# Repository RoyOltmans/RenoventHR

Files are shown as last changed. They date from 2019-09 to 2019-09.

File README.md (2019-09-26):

# RenoventHR

All rights of the Mechenical ventelation system are owned by Renovent.

This is a reverse engeneered control device to remotely control and automate ventilation at home.

**Usage of this project is on your own risk.**

# Results

Some screenshot of the final endresult

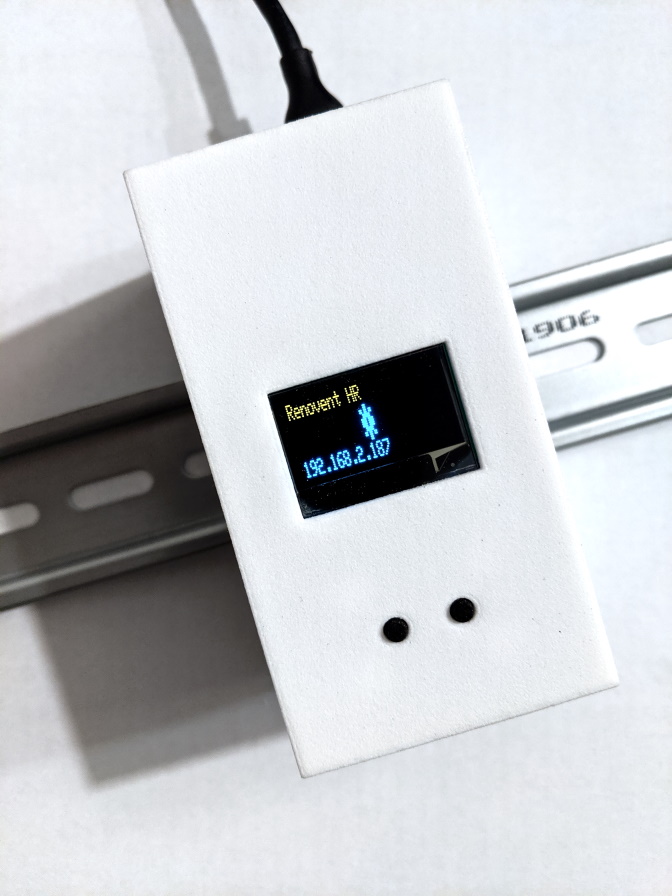
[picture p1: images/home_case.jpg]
home_case


Bottom view case

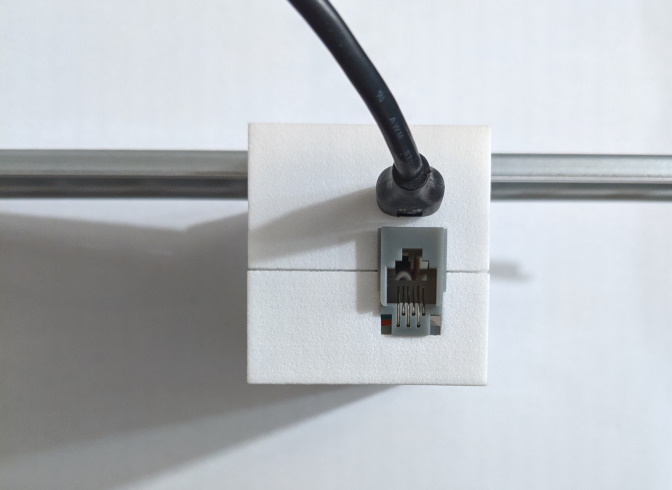
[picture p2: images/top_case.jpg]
top_case


Side view case

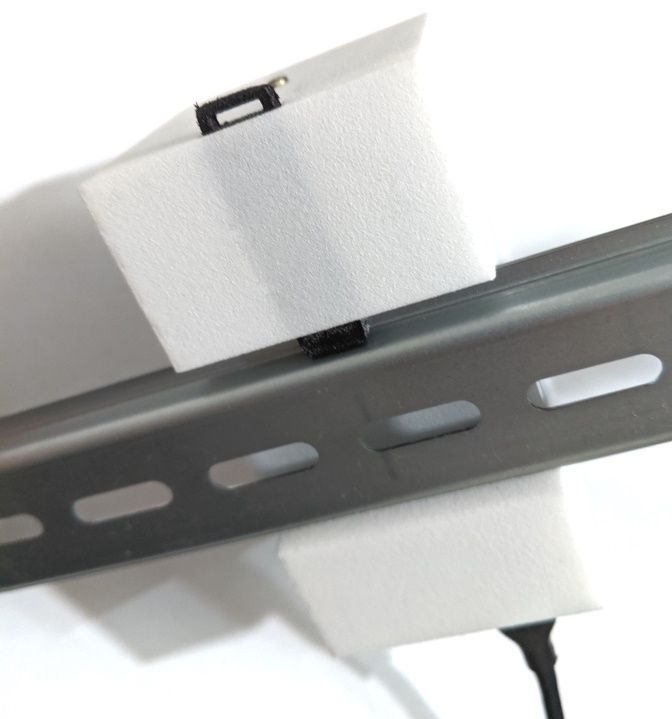
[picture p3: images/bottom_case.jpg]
bottom_case


Bottom view case

# Motivation

Connected RenoventHR Module to switch a mechanical ventilation heat recovery system from Renovent HR.

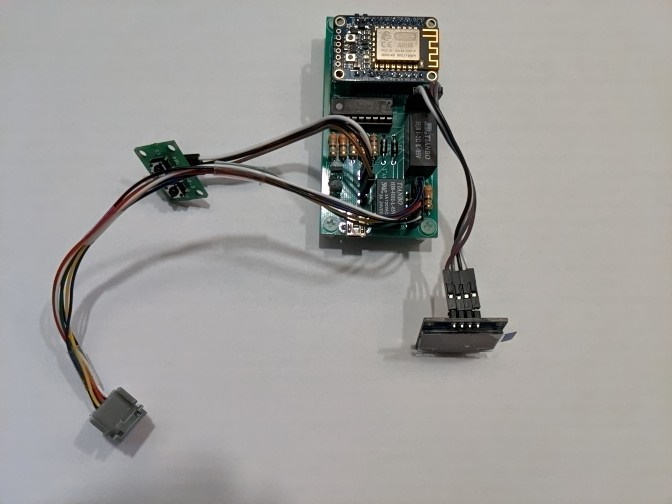
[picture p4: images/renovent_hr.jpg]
renovent_hr


I was first inspired by a friend whom wanted to switch his mechanical ventilation. He has a Renovent setup and he could use a RF solution.
That started me thinking let’s try this myself, off course I have a different setup that’s a little more complicated because of the heat recovery.

After an evening of googling I found a site of an old classmate (what a small world) Ingmar Verheij. His journey is the same as mine, but he already solved it (https://www.ingmarverheij.com/bediening-wtw-altijd-op-de-verkeerde-plek/).

He posted a solution on git but did not finish a tutorial, so I thought I could solve this quickly. After approximately half a year I can say I finished reverse engineering the setup and build the whole project with a 3D printed case (still in backorder).

I refactored the code (separated code, minified web and altered some functionality so the interaction should work) to my taste and added a few configuration hacks. 
Changes made were approximately:
 - Minified HTML (minimize System footprint)
 - Further restructured and optimized code
 - Added manual config (personal taste)
 - Separated Core, Data, Interfacing and tools (not fully)
 - Removed intmode/pinmode (secondary in total)
 - Added/rebuild button, startup, filter functions
 - Restructured code
 - Changed MCP calls intMode to pinMode
 - Added manual WIFI configuration trough config file

Also, the reverse engineering of the electronics created a lot of issues. The original part list provided left out crucial info for the relays. I almost stopped because I couldn’t fix it, after measuring everything and re-checking (going back in the books) I discovered that the pictures of the relays on the site were not the correct voltage. The part list in the bottom are all the correct parts. Be careful with the rj12 jack, if you use a different form factor it maybe will not fit in the case (adjust the case according with fusion 360).

So, to let you wait further let’s go into the build.

# Building the code
The code needs to be compiled with preferably the Arduino IDE version 2.4.1 below the settings:

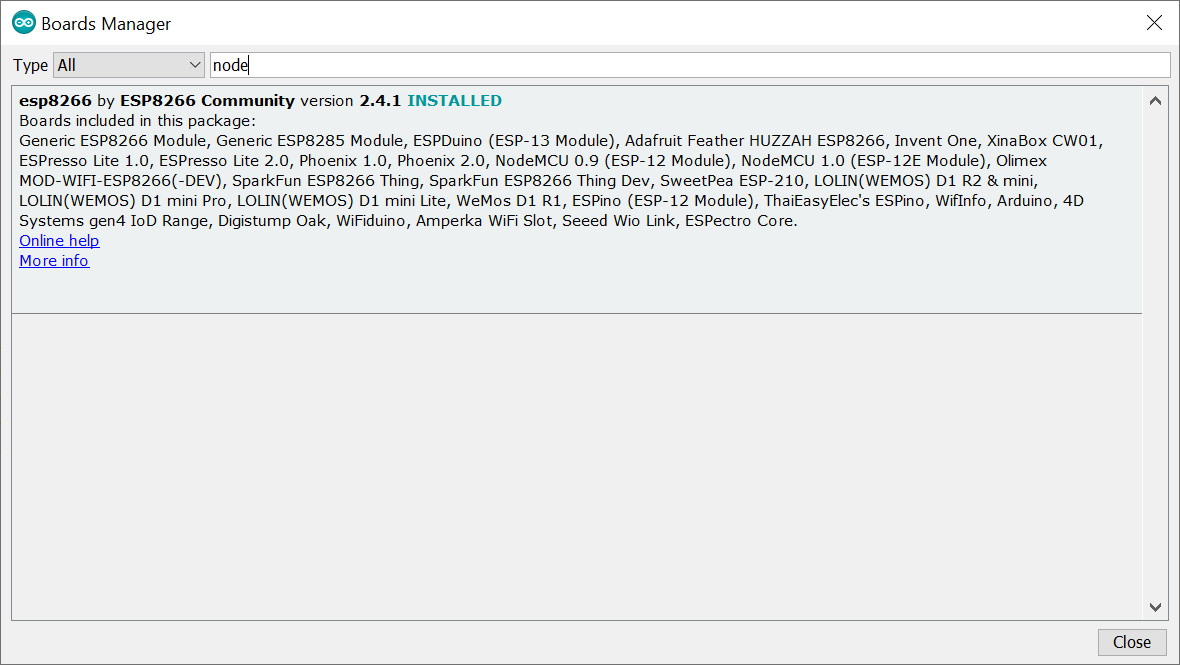
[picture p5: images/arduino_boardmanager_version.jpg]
arduino_boardmanager_version
 
Set the compiler to use the right version 2.4.1 of nodemcu ESP firmware build tools. 

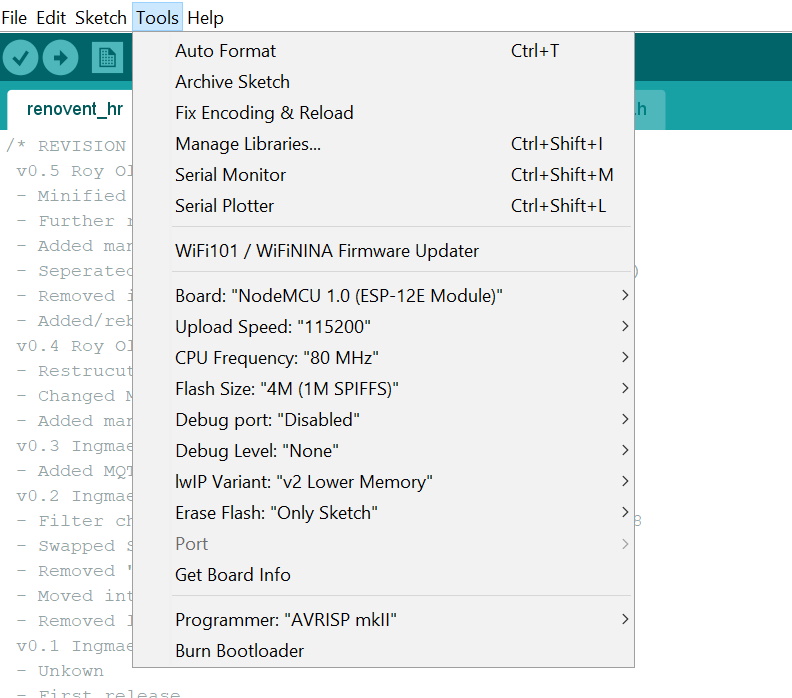
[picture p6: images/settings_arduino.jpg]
settings_arduino
 
Set the correct settings for the HUZZAH board for uploading the compiled code.

I also added the working libraries, after a lot of juggling I figured these are the used standard libs:
https://github.com/RoyOltmans/RenoventHR/tree/master/lib

For flashing the HUZZAH via a normal usb cable use the correct sequence of buttons to get in program mode. If I remember correctly, GPIO0 must be low while booting: press and hold the reset button. press and hold the program button. release the reset button, the HUZZAH will boot in program mode.

# Case
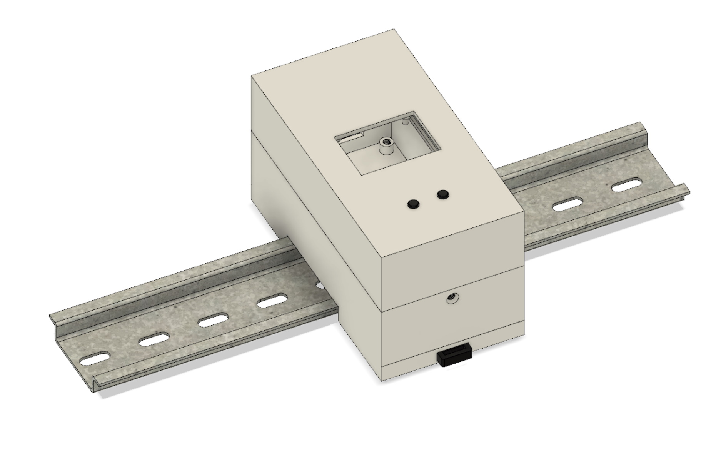
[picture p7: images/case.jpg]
case
 To build the case use the following STL files in this location https://github.com/RoyOltmans/RenoventHR/tree/master/bin/3D%20Models%20STL

I have also added the Fusion 360 (from autodesk https://www.autodesk.com/products/fusion-360/students-teachers-educators) file so you can edit the case (please do not judge my CAD skills).

You will need to get a DIN rail to mount the case on and if you prefer as I do a 5-volt din rail power source. 
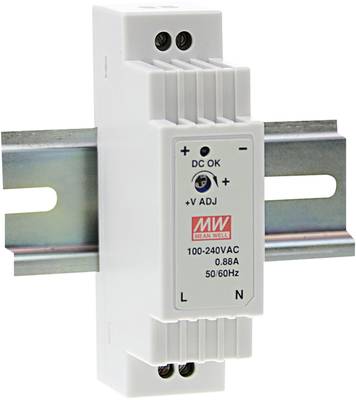
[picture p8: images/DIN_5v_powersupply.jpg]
DIN_5v_powersupply


See Mean Well DR-15-5 DIN-rail 5 V/DC2.4A 12W (https://s.click.aliexpress.com/e/mliRreY0)

# PCB's
To build the project firstly you need to order the PCB design via for example seeed studio, they can process eagle schema (in the repository).

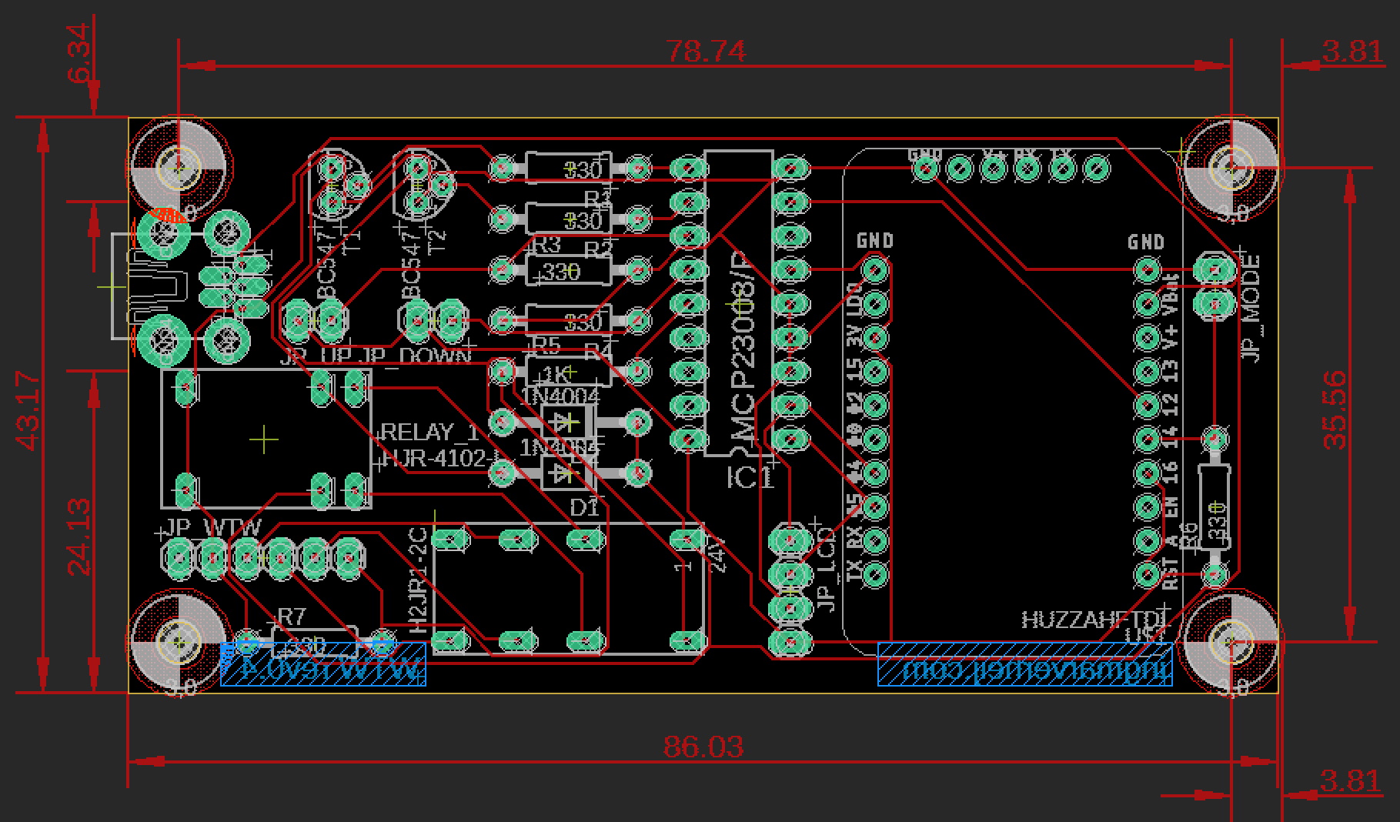
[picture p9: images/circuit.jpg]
circuit

The primary pcb:
https://github.com/RoyOltmans/RenoventHR/tree/master/pcb/EAGLE/RenoventHR%20v0.4

I ordered this board on https://www.seeedstudio.com/ was very happy with end result and the price.
To edit the board you will need Eagle (from autodesk https://www.autodesk.com/products/eagle/free-download) you can download this freely.

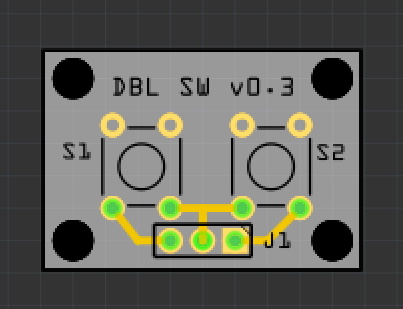
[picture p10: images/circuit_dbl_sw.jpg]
circuit_dbl_sw


The double switch pcb:
https://github.com/RoyOltmans/RenoventHR/tree/master/pcb/Fritzing/Double%20Tactile%20Switch%20v0.3

I ordered this board directly via the tool, also very good service, price and quick (https://aisler.net/partners/fritzing).
To edit this board you will need fritzing you can download this for free (https://fritzing.org/home/).

# Pinlayout

Every connector PCB printed text should be horizontally aligned to number the pins, pin 1 itterating every pin plus 1 afterwards are the pin numbers.

LCD pinlayout
```
-----------------
JP_LCD PINS
Pin   1   2   3   4
      |   |   |   |
Pin  VCC GND SCL SDA
Connected to LCD 
-----------------
```
Switch Pinlayout
```
-----------------
JP_UP PINS:

Pin    1         2 
       |         |
Pin    -     Left Pin
JP_1 on DBL SW PCB
-----------------
JP_DOWN PINS
Pin    1         2 
       |         |
Pin Center Pin  Right Pin
JP_1 on DBL SW PCB
-----------------
```

WTW RJ12 connector
```
-----------------
JP_WTW PINS
  1     2    3    4      5    6
  |     |    |    |      |    |
White Black Red Green Yellow Blue
RJ12 Color coding
-----------------
```

# Tools
Personally, I solder with a soldering tip Pencil shape size 0.4 mm, this worked perfectly. 

Good tools are half of the work, new tip, good soldering paste (wire), magnifying glass etc.

# SMART-HUB - Home Assistant
For details on connecting to the HA, I suggest looking at the site of Ingmar https://www.ingmarverheij.com/built-smart-heat-recovery-system/

Be careful I changed the MQTT paths and these are accessible via the config file. I will repost them below:
```
/*-------------------MQTT topics-------------------*/
#define Gateway_Name "RenoventHR"
#define Base_Topic "home/"
#define MQTT_GetState_Topic Base_Topic Gateway_Name "/getWTWstate"
#define MQTT_State_Topic Base_Topic Gateway_Name "/wtwState"
#define MQTT_FilterState_Topic Base_Topic Gateway_Name "/changeFilter"
#define MQTT_SetState_Topic Base_Topic Gateway_Name "/setWTWstate"

#define MQTT_Standard_Topic Base_Topic Gateway_Name
```

After some tinkering I have decided to add a short totorial of the implementation in Home Assistant. Notice you will MQTT to get this fully operational.

Firstly I must give credits to **Ingmar Verheij** for researching the HA connectivity and the custom fan card support for HA by **finity69x2**, see his github for the original JS script *https://github.com/finity69x2/fan-control-entity-row*.

To start of, I am using a older version of **HA version 0.86.4**. *Be aware this can work differently on your version of HA.*

Firstly you will need to upload a javascript in to the `www` folder of the configuration root of home-assistant (your .yaml are also located here). If this folder does not exist create it. 

On linux you can do the following steps:
```
mkdir www
wget https://raw.githubusercontent.com/RoyOltmans/RenoventHR/master/code/Home%20Assistant/www/fan-control-entity-row.js
```

After you have done this on older version of HA you need to edit ui-lovelace.yaml (this does not work if you created a lovelace interactive version.

In ui-lovelace.yaml you will need to add the following below `resources`
```
  - url: /local/fan-control-entity-row.js
    type: js
```

If this does not work you can try to open the raw editor of lovelace and add the following at the top: 
```
resources:
  - type: js
    url: /local/fan-control-entity-row.js
```

Once your finished add a new file to the configuration root of home assistant. Use the follwoing command for that
```
wget https://raw.githubusercontent.com/RoyOltmans/RenoventHR/master/code/Home%20Assistant/fan.yaml
```

Onze you have done all these staps restart home assistant fully, this will reload and add the fan control of the WTW via MQTT.

Onze you have finished this you can add the following card to your lovelace dashboad. You can do this by toggling the editor and adding a card manualy via the lovelace configurator in HA.

```
entities:
  - customTheme: true
    entity: fan.wtw_mechanic_ventilation
    name: WTW Renovent HR
    type: 'custom:fan-control-entity-row'
    show_header_toggle: false
title: Mechinical Ventilation
type: entities
```

Below a screenshot of the card in Home Assistant.
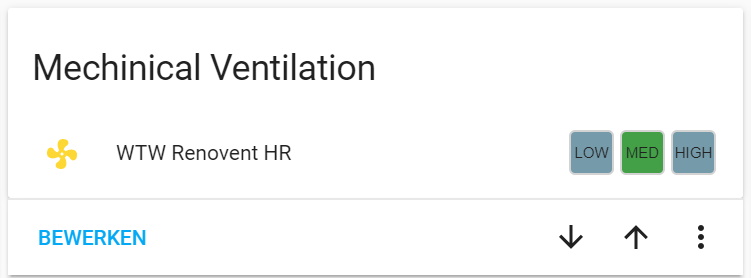
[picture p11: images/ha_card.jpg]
ha card


Once you have added the fan you can control the fan levels via sesnors and automations you have designed yourself. Ingmar also described a way to add a notification for cleaning the filters. Please see his tutorial for further info.

# Configuration and Software
For configurations, you can follow the description on https://www.ingmarverheij.com/built-smart-heat-recovery-system/
The software as written by Ingmar is still operational, you can interact directly with the device. Or you can couple it through a smart hub via MQTT as described above.

Or edit the config.h file adding your personal configurations, below you will find the details of the config.h:
```
/*-------------------General----------------------*/
const char* Version = "0.5";

/*-------------------WIFI Settings----------------*/
String APssid = "SSID WIFI";
String APpassword = "PASSWORD WIFI";

/*-------------------MQTT Settings-------------------*/
String mqtt_user = "your_username"; // not compulsory only if your broker needs authentication
String mqtt_pass = "your_password"; // not compulsory only if your broker needs authentication
String mqtt_server = "MQTT SERVER NAME or IP";
long mqtt_port = strtol("1883",NULL,10);

/*-------------------MQTT topics-------------------*/
#define Gateway_Name "RenoventHR"
#define Base_Topic "home/"
#define MQTT_GetState_Topic Base_Topic Gateway_Name "/getWTWstate"
#define MQTT_State_Topic Base_Topic Gateway_Name "/wtwState"
#define MQTT_FilterState_Topic Base_Topic Gateway_Name "/changeFilter"
#define MQTT_SetState_Topic Base_Topic Gateway_Name "/setWTWstate"

#define MQTT_Standard_Topic Base_Topic Gateway_Name
```

# Part list
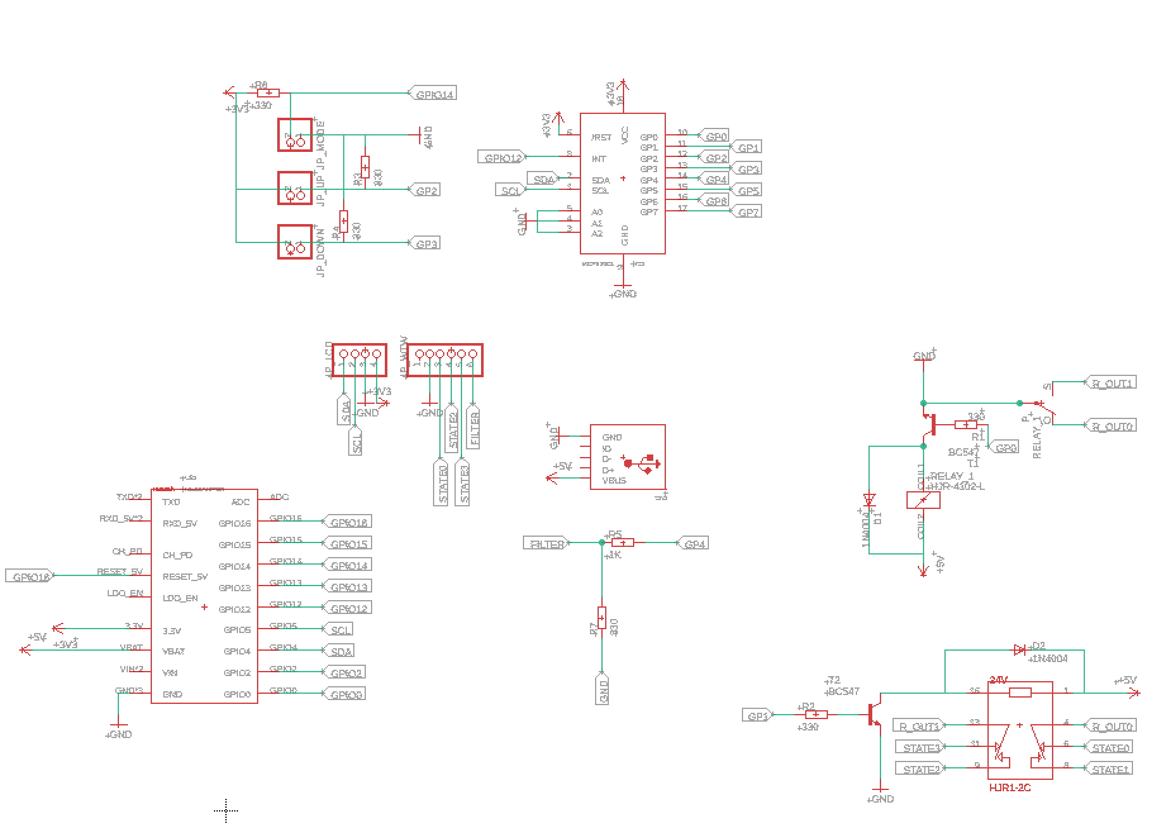
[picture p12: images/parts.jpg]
parts

- hjr-4102-l 1x Miniature relay HJR-4102-L-05VDC-S-Z (order at Conrad (EU))
- hjr1-2c 1x Miniature relay HJR1-2C-L-05VDC (order at Conrad (EU))
- ic-18 1x IC base 18 pins (order at Conrad (EU))
- jumper 1x Jumper black open (Jumper zwart open) (order at Conrad (EU))
- resistor330 6x Carbon film resistance 0,5W 0411 330Ohm (Koolfilmweerstand 330Ω Axiaal bedraad 0411 0.5 W 5) (order at Conrad (EU))
- resistor1k 1x Carbon film resistance 0,5W 0411 1KOhm (Koolfilmweerstand 1 kΩ Axiaal bedraad 0411 0.5 W 5 ) (order at Conrad (EU))
- connector 1x Bus, horizontal installation MUB1B5W 1 Port econ connect (order at Conrad (EU))
- maleheader1x Würth Elektronik Male header (order at Conrad (EU))
- femaleheader1x Würth Elektronik Female header (standard) WR-PHD Total poles 10 grid size: 2.54 mm 61301011821 (order at Conrad (EU))
- mcp230081x Microchip Technology MCP23008-E/P Interface-IC - I/O expansion POR I²C 1.7 MHz PDIP-18 (order at Conrad (EU))
- bc547a 2x Diotec BC547A Transistor (BJT) - discreet TO-92 1 NPN (order at Conrad (EU))
- 1n4004 2x Diotec Si-rectifier diode 1N4004 DO-204AL 400 V 1 A (order at Conrad (EU))
- adafruit_HUZZAH_ESP8266_lq1x Adafruit HUZZAH ESP8266 Breakout (https://www.adafruit.com/product/2471)
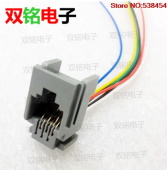
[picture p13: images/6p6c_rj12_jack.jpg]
6p6c_rj12_jack
-  1x rj12 jack with cables and sleeve for case (https://s.click.aliexpress.com/e/ExAocZHe)
- 096inch_128X64_YellowBlue_OLED_Display_Module 1x 0.96inch 128X64 Yellow Blue OLED Display Module (https://s.click.aliexpress.com/e/39m65cSM)
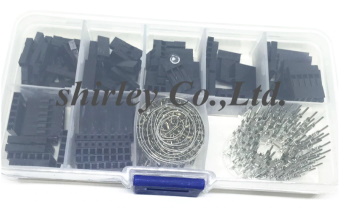
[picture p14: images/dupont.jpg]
dupont
-  Dupont Wire Jumper Pin Header Connector (https://s.click.aliexpress.com/e/3WbYzW3I)
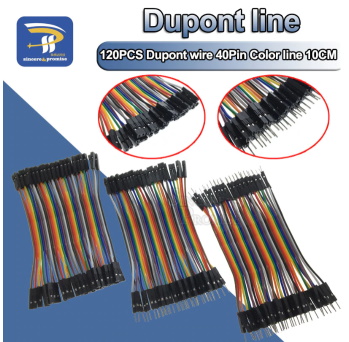
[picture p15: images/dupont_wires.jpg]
dupont_wires
- Dupont Wires (https://s.click.aliexpress.com/e/KMFFxgfe)
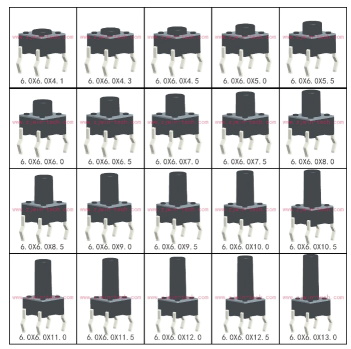
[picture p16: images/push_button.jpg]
push_button
-  A generic pushbutton (https://s.click.aliexpress.com/e/kaTmlRJw)

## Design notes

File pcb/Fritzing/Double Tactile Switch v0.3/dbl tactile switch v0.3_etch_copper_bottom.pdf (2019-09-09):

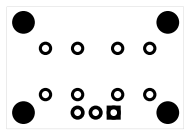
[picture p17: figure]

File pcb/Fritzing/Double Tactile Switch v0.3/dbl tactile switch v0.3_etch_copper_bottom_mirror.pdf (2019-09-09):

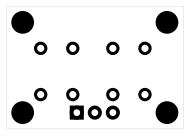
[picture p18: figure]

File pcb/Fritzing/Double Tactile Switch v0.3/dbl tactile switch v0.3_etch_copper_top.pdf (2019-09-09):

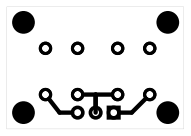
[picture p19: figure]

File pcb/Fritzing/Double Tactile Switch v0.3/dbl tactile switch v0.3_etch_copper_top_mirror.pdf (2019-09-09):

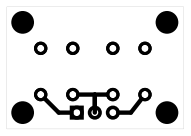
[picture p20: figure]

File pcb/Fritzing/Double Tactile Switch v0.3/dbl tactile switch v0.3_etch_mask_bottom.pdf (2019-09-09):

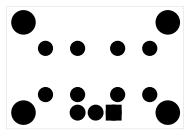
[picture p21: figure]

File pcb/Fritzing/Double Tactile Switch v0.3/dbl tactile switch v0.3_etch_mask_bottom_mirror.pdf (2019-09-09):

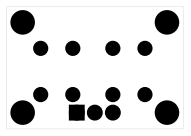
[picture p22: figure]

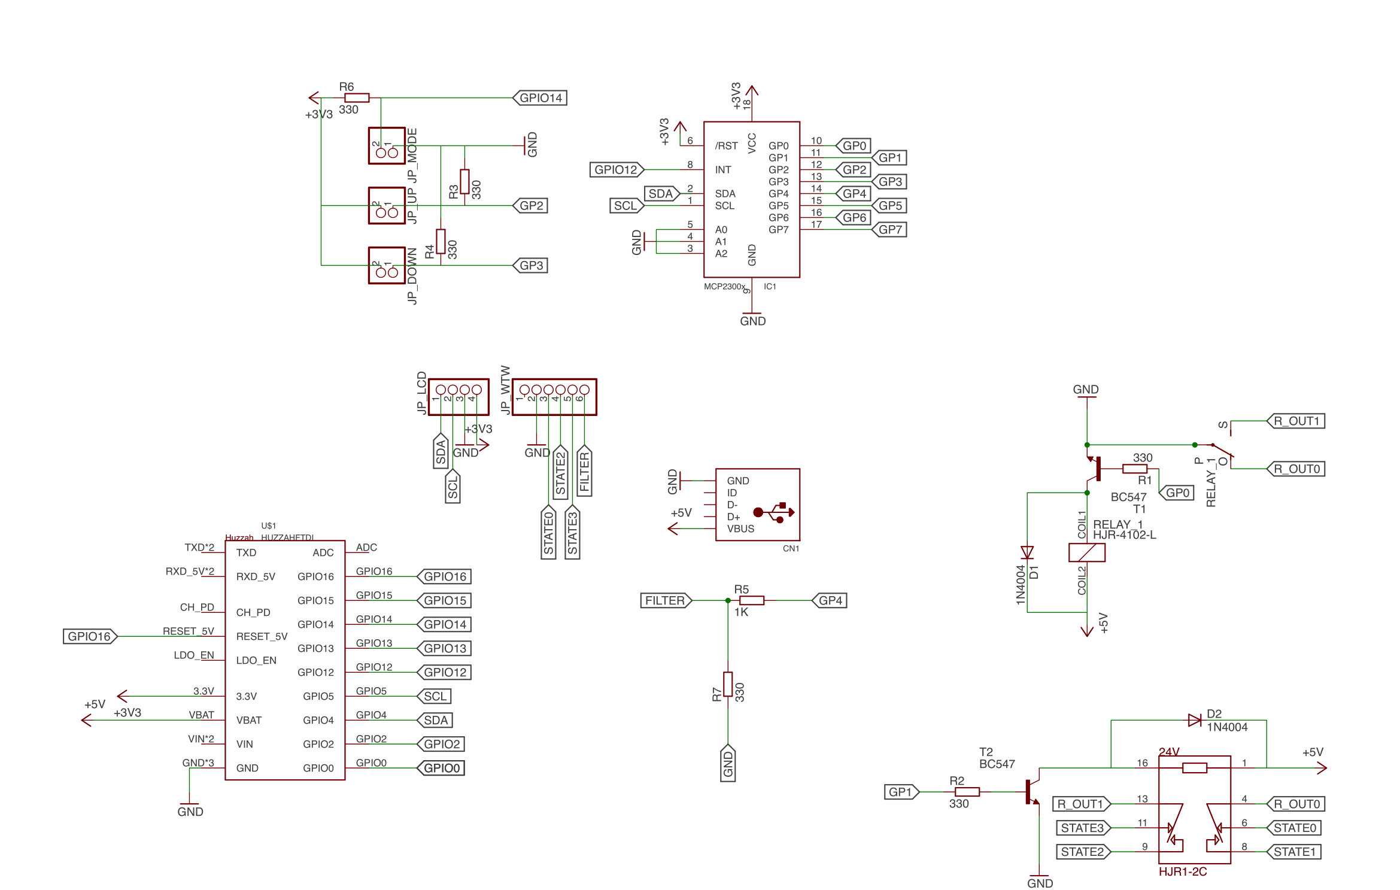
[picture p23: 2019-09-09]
pcb/EAGLE/RenoventHR v0.4/Image-Schematic.png

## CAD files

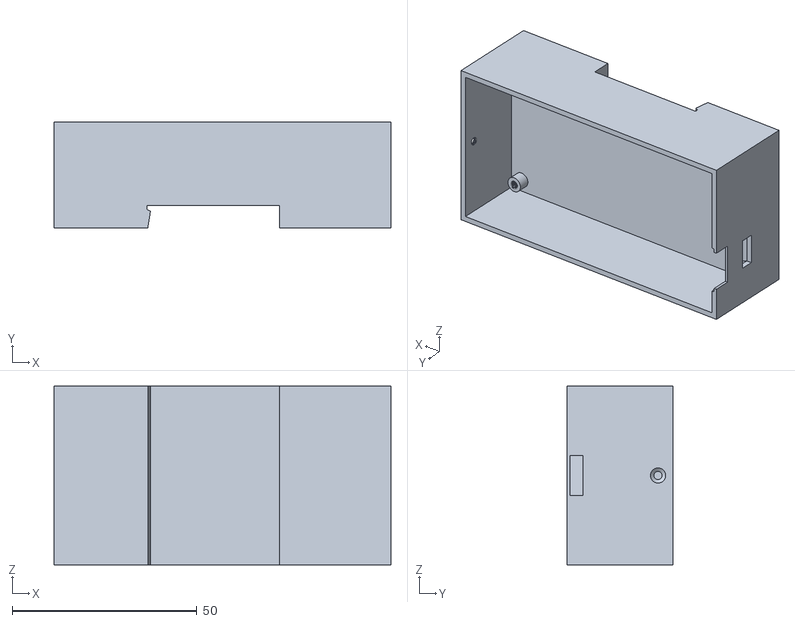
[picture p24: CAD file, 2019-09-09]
bin/3D Models STL/Bottom Case.stl
91.2 x 28.6 x 48.5

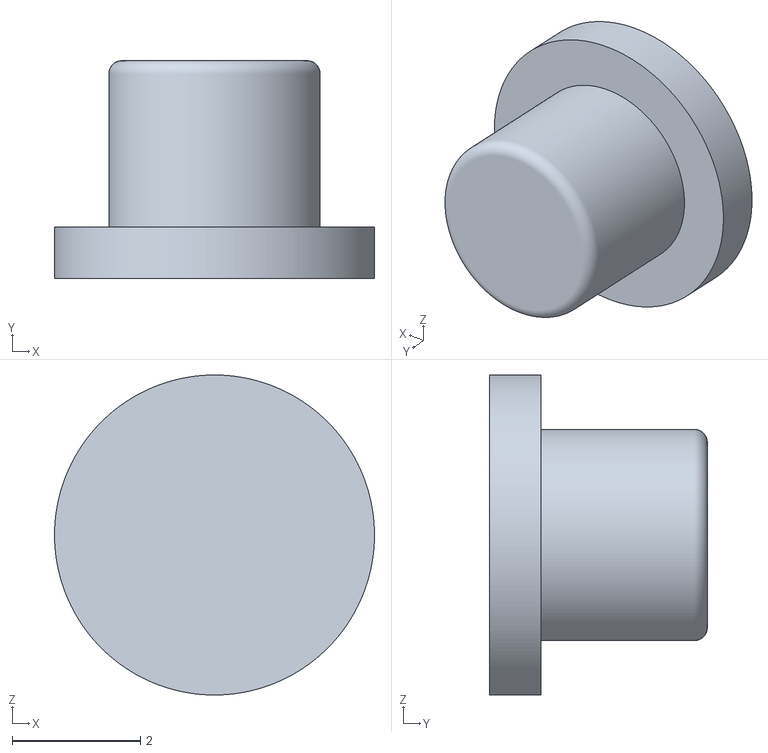
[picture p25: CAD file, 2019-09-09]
bin/3D Models STL/Button Left.stl
5.00 x 3.40 x 5.00

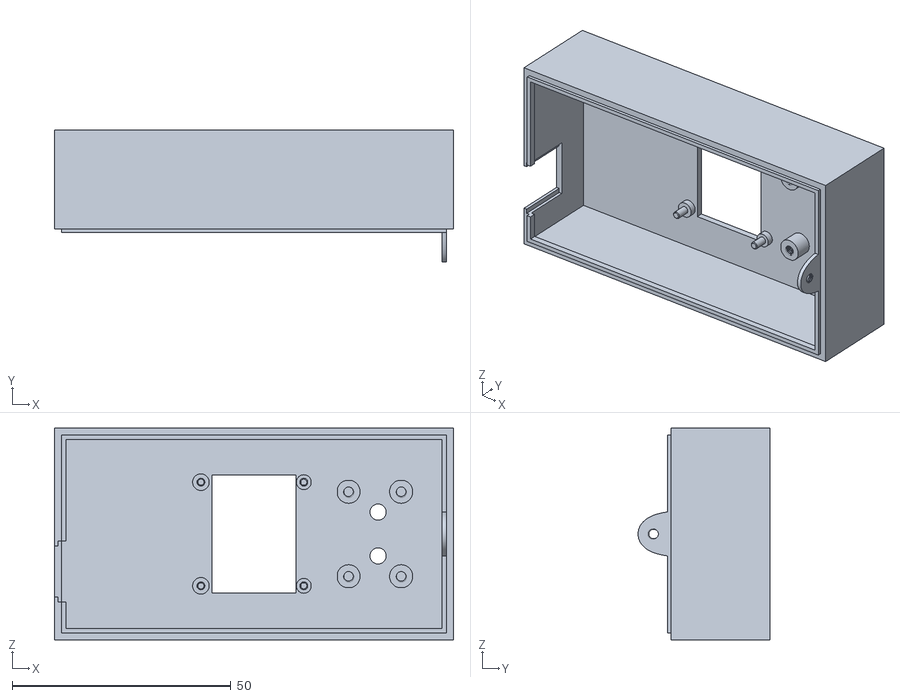
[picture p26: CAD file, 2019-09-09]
bin/3D Models STL/Top Case.stl
91.2 x 30.2 x 48.5

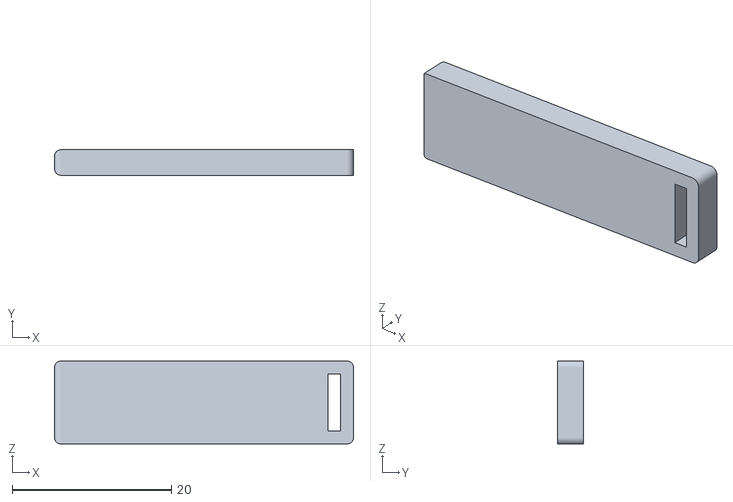
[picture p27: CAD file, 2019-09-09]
bin/3D Models STL/Clip.stl
37.5 x 3.20 x 10.4

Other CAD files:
bin/3D Models STL/Button Right.stl
3D model/Renovent HR Case Version 3.1 v3.f3d

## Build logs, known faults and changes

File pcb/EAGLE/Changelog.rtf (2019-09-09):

Rev 0.4
- Added pull down resistor for FILTER
- Changed package of mini USB to match physical layout

Rev 0.3
- Swapped STATE2 and STATE3 (just for visuals, was already done in code)

Rev 0.2
- Swapped collector and emitter on T1 and T2 (to relay)
- Added mini-USB +5V bus for power (VBAT) and relays
- Renumbered the resistors (was unlogical)
- Included 3mm drill holes
- Added text on back - ingmarverheij.com
- Added text on back - WTW rev0.2
(- Used RJC-4102 instead of RJC-4102-E)

Rev 0.1
- Initial version

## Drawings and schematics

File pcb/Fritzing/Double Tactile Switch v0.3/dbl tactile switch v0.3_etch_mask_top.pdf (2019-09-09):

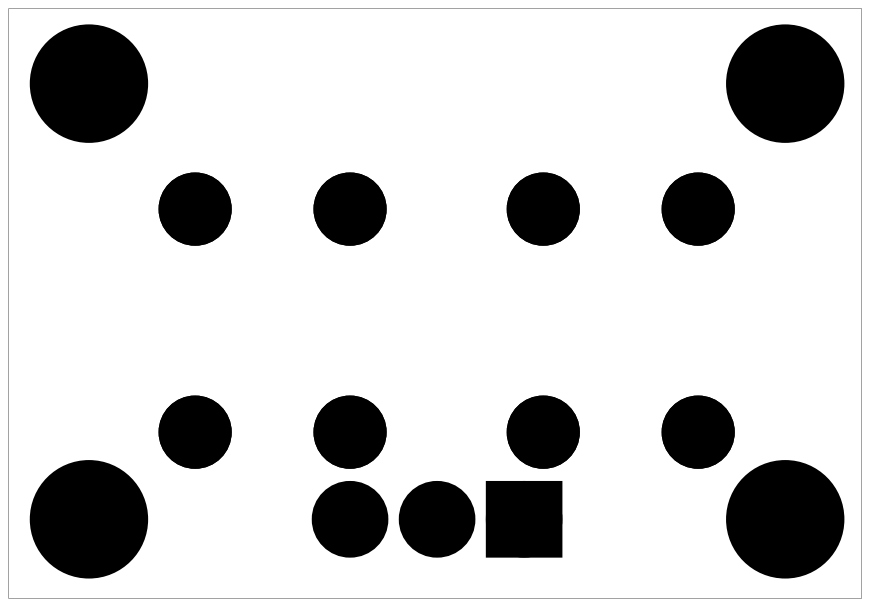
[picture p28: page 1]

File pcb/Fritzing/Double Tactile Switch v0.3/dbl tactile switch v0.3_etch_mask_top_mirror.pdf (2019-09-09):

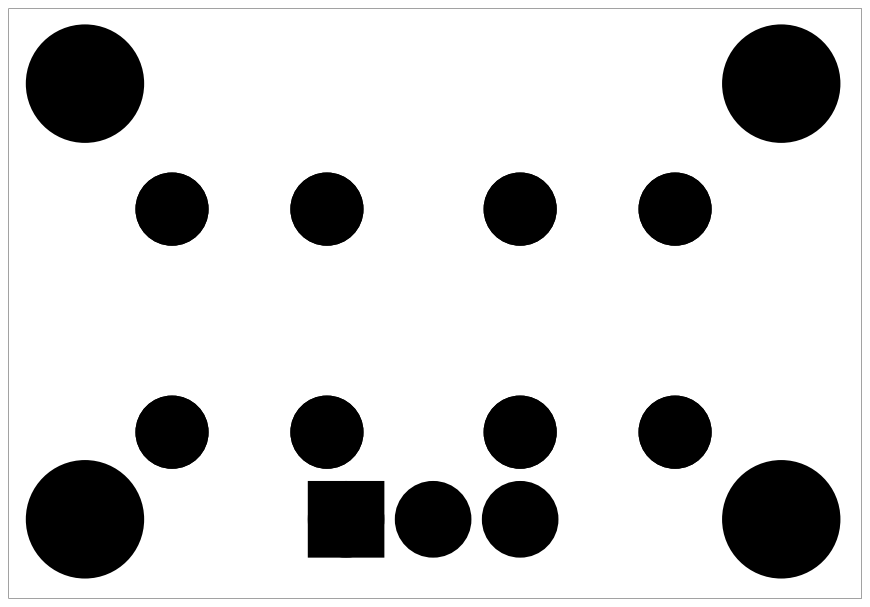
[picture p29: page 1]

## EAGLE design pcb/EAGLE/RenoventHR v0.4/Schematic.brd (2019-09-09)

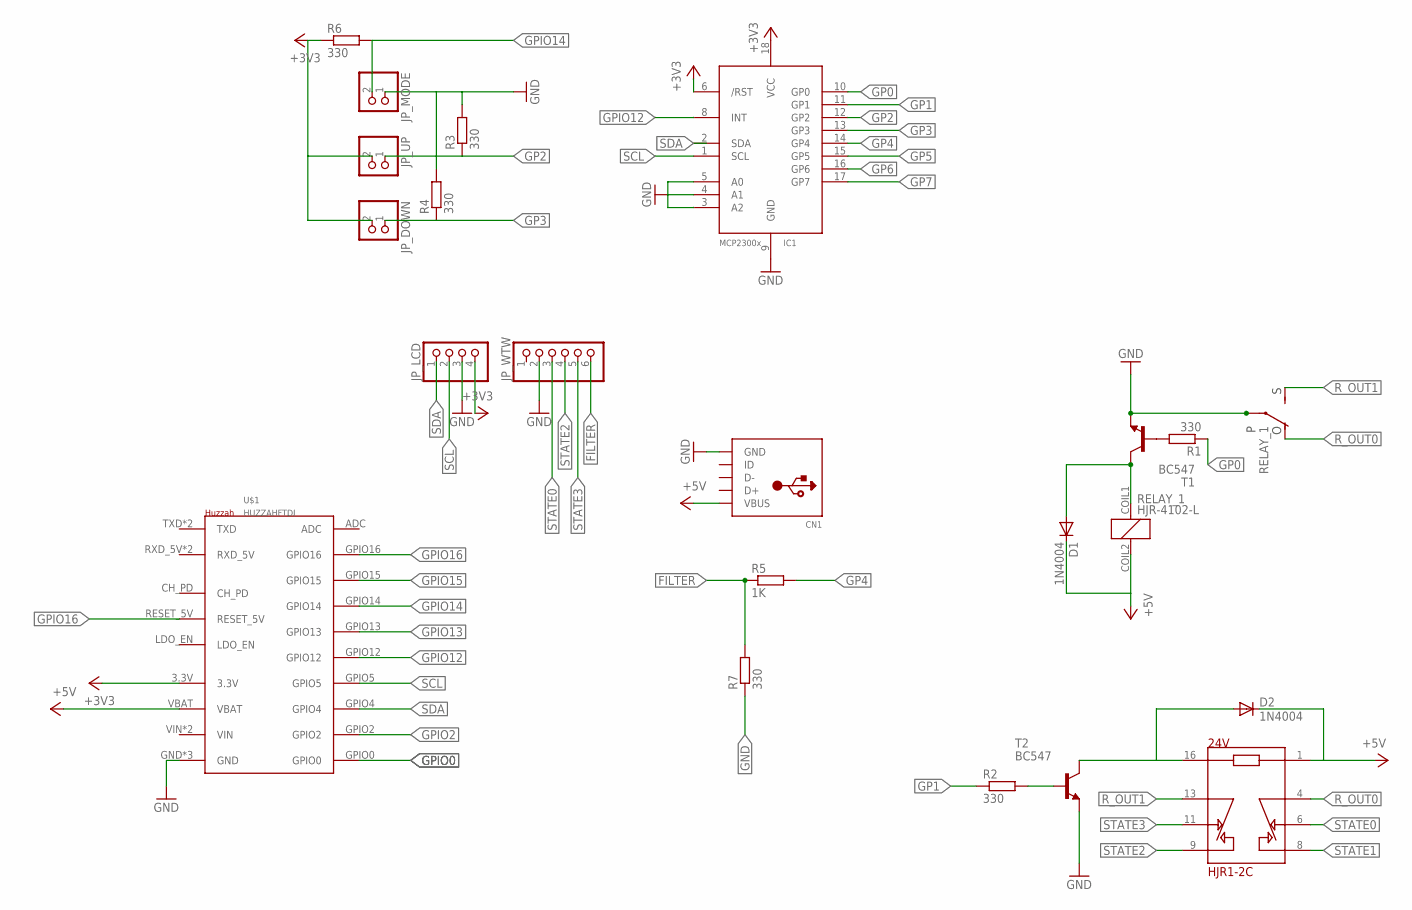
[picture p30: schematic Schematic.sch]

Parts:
CN1: USBTHM; USB-MINIB-THM
D1, D2: 1N4004; DO41-10
IC1: MCP23008/P; DIL18
JP_DOWN: PINHD-1X2; 1X02
JP_LCD: PINHD-1X4; 1X04
JP_MODE: PINHD-1X2; 1X02
JP_UP: PINHD-1X2; 1X02
JP_WTW: PINHD-1X6; 1X06
R1, R2, R3, R4, R6, R7: 330; 0207/10
R5: 1K; 0207/10
RELAY_1: HJR-4102-L; HJR4102
RELAY_2: HJR1-2C
T1, T2: BC547; TO92
U$1: HUZZAHFTDI; HUZZAH-FULL

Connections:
+3V3: IC1.6 (/RST), IC1.18 (VCC), JP_DOWN.2, JP_LCD.4, JP_UP.2, R6.1, U$1.3.3V
+5V: CN1.VBUS, D1.C, D2.C, RELAY_1.COIL2 (2), RELAY_2.1, U$1.VBAT
FILTER: JP_WTW.6, R5.1, R7.2
GND: CN1.GND, IC1.3 (A2), IC1.4 (A1), IC1.5 (A0), IC1.9 (GND), JP_LCD.3, JP_MODE.1, JP_WTW.2, R3.2, R4.2, R7.1, RELAY_1.CENTER1, RELAY_1.CENTER2 (P2), T1.1 (E), T2.1 (E), U$1.GND, U$1.GND2 (GND), U$1.GND3 (GND)
GP0: IC1.10 (GP0), R1.1
GP1: IC1.11 (GP1), R2.1
GP2: IC1.12 (GP2), JP_UP.1, R3.1
GP3: IC1.13 (GP3), JP_DOWN.1, R4.1
GP4: IC1.14 (GP4), R5.2
GP5: IC1.15 (GP5)
GP6: IC1.16 (GP6)
GP7: IC1.17 (GP7)
GPIO0: U$1.GPIO0
GPIO2: U$1.GPIO2
GPIO12: IC1.8 (INT), U$1.GPIO12
GPIO13: U$1.GPIO13
GPIO14: JP_MODE.2, R6.2, U$1.GPIO14
GPIO15: U$1.GPIO15
GPIO16: U$1.GPIO16, U$1.RESET_5V
unnamed: R1.2, T1.2 (B)
unnamed: R2.2, T2.2 (B)
R_OUT0: RELAY_1.CON2OPTION (O), RELAY_2.4
R_OUT1: RELAY_1.CON1DEFAULT (S), RELAY_2.13
SCL: IC1.1 (SCL), JP_LCD.2, U$1.GPIO5
SDA: IC1.2 (SDA), JP_LCD.1, U$1.GPIO4
STATE0: JP_WTW.3, RELAY_2.6
STATE1: RELAY_2.8
STATE2: JP_WTW.4, RELAY_2.9
STATE3: JP_WTW.5, RELAY_2.11
T1_RELAY1: D1.A, RELAY_1.COIL1 (1), T1.3 (C)
T2_RELAY2: D2.A, RELAY_2.16, T2.3 (C)

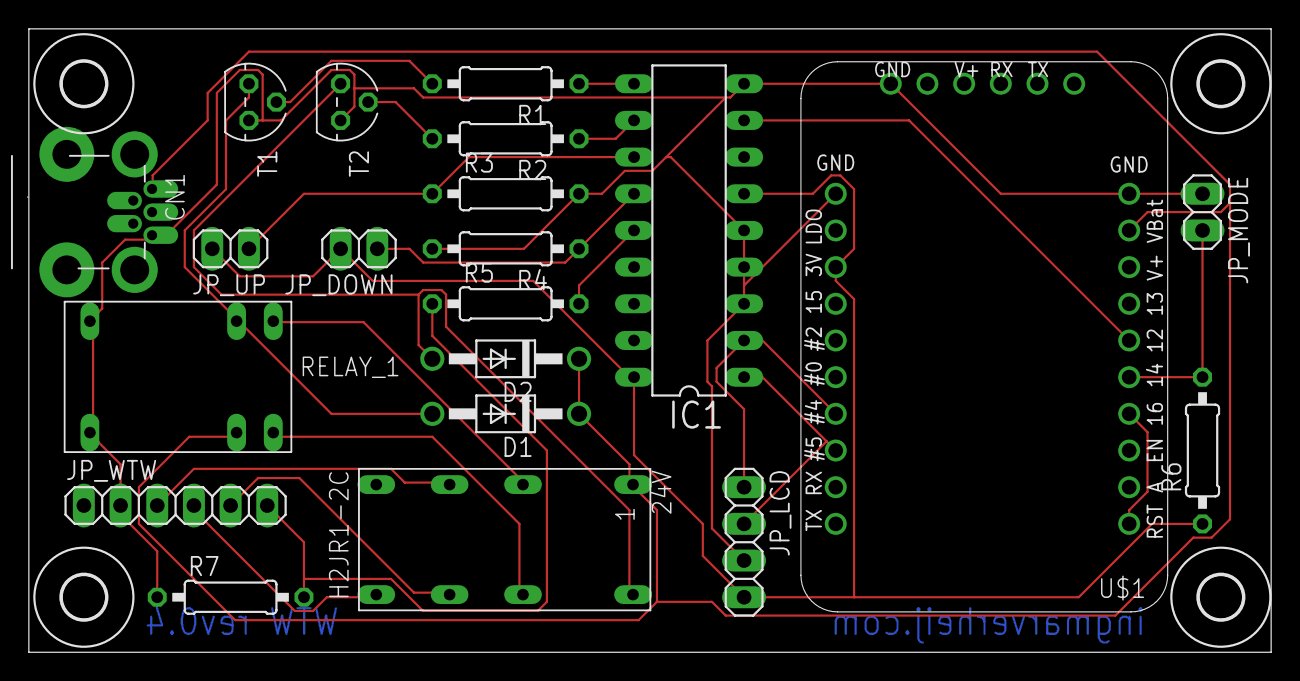
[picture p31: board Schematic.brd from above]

Board: 2 copper layers, 86.0 x 43.2 mm, 25 parts (0 on the bottom side), 23 nets.

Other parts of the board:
U$2, U$3, U$4, U$5: 3,0

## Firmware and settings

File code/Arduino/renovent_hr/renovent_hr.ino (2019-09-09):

/* REVISION
 v0.5 Roy Oltmans
 - Minified HTML
 - Further restructured and optimized code
 - Added manual config
 - Seperated Core, Data, Interfacing and tools (not fully)
 - Removed intmode/pinmode (secondary in total)
 - Added/rebuild button, startup, filter functions
 v0.4 Roy Oltmans
 - Restrucutered code
 - Changed MCP calls intMode to pinMode
 - Added manual WIFI configuration trough config file
 v0.3 Ingmaer Verheij
 - Added MQTT interface
 v0.2 Ingmaer Verheij
 - Filter change was read from ESP8266 instead of MCP23008
 - Swapped STATE2 with STATE3
 - Removed "Master" in naming
 - Moved interrupts to last action in setup
 - Removed legacy code
 v0.1 Ingmaer Verheij
 - Unkown
 - First release 
*/

/*-------------------Include Standard libraries----------------*/
#include <ESP8266WiFi.h>
#include <ESP8266WebServer.h>
#include <ESP8266mDNS.h>
#include <EEPROM.h>
#include <ArduinoJson.h>
#include <PubSubClient.h>
#include <SPI.h>                                                         // Required for OLED
#include <Wire.h>                                                        // Required for OLED
#include <Adafruit_GFX.h>                                                // Required for OLED
#include <Adafruit_SSD1306.h>                                            // Required for OLED
#include <Adafruit_MCP23008.h>                                           // Port Expander

/*-------------------Loading User Configuration----------------*/
#include "config.h"

/*-------------------Var preperation----------------*/
String eepromSSID;
String eepromPassword;
String eepromMQTT;
String content;
int statusCode;
bool ButtonPinUpState;
bool ButtonPinDownState;
bool FilterState;
int FilterChangePinState = 0;
bool startupMode;                       // false = Normal mode, true = Config mode
const char* NodeName = "Renovent HR";
const char* SSIDsetup = "RenoventHR";
/*-------------------Var WTW state----------------*/
volatile int currentState;   
volatile int changeFilter = false;
volatile int buttonState = 0;
#define buttonStateMin 0
#define buttonStateMax 3
/*-------------------Var GPIO on ESP8266----------------*/
#define PIN_OLED_RESET    20            // Something which isn't connected
#define PIN_PE_int        12            // Interrupt for port extender
#define PIN_startupmode   14            // Startup mode (setup or normal)
#define PIN_reset         16            // Connected to reset pin
/*-------------------Port extender----------------*/
#define PIN_relay1         0            // On port expander 
#define PIN_relay2         1            // On port expander
#define PIN_button_up      2            // Button up
#define PIN_button_down    3            // Button down
#define PIN_FilterChange   4            // Filter change indicator
/*-------------------Var EEPROM----------------*/
#define eepromSSIDstart    0            //  0 - 31  = SSID
#define eepromSSIDend     31            //
#define eepromPASSstart   32            // 32 - 95  = Passprhase
#define eepromPASSend     95            //
#define eepromWTWaddr     96            // 96       = wtwState
#define eepromMQTTstart   97            // 97 - 352 = MQTT broker
#define eepromMQTTend    352            //
/*-------------------Var MQTT----------------*/
#define MQTTpublishInterval  60         // MQTT Interval in seconds to publish value
#define MQTTretryInterval    60         // MQTT Interval in seconds to retry MQTT connection
long lastMQTTmsg   = millis() + (MQTTpublishInterval * 1000); 
long lastMQTTretry = millis() + (MQTTretryInterval   * 1000); 

/*-------------------Loading Libs----------------*/
MDNSResponder mdns;
ESP8266WebServer server(80);
WiFiClient espClient;
Adafruit_SSD1306 display(PIN_OLED_RESET);           // OLED 0.96 128x64 i2C (at 0x3C)
PubSubClient mqttClient(espClient);                 // Loading PubSubClient
Adafruit_MCP23008 mcp;                              // Port expander MCP23008

/*-------------------Loading custom----------------*/
#include "data.h"
#include "toollib.h"
#include "corelib.h"
#include "interface.h"

void setup() {
  // Begin Serial
  Serial.begin(115200);
  Serial.println("");
  Serial.println("Booting...");
  
  // Setup pins
  Serial.print(F("GPIO...")); delay(100);
  mcp.begin(); // Start port expander
  Serial.print(F("Port expander started"));
  pinMode(PIN_reset, OUTPUT);
  digitalWrite(PIN_reset, HIGH); // Pull-up resistor
  pinMode(PIN_PE_int, INPUT);
  pinMode(PIN_startupmode, INPUT); // Determine startup mode 
  mcp.pinMode(PIN_relay1, OUTPUT);
  mcp.pinMode(PIN_relay2, OUTPUT);
  mcp.pinMode(PIN_button_up, INPUT); // Button up
  mcp.pinMode(PIN_button_down, INPUT); // Button down
  mcp.pinMode(PIN_FilterChange, INPUT); // Filter change indicator
  mcp.digitalWrite (PIN_relay1, HIGH);
  delay(2000);
  mcp.digitalWrite (PIN_relay1, LOW);
  Serial.println("[DONE]");
  
  // OLED
  Serial.print(F("OLED..."));
  display.begin(SSD1306_SWITCHCAPVCC, 0x3C);                          // Initialize with the I2C addr 0x3C (for the 128x32)
  display.clearDisplay();
  display.setTextSize(1);
  display.setTextColor(WHITE);
  display.setCursor(0, 0);
  display.print(NodeName);
  display.print(F("   Ver:"));
  display.println(Version);
  display.println(F(""));
  display.println(F("   ...starting..."));
  display.display();
  delay(2000);
  display.clearDisplay();
  display.setTextSize(1);
  display.setTextColor(WHITE);
  display.setCursor(0, 0);
  Serial.println(F("initialized")); delay(100);
  
  // Determine startup mode
  startupMode = (bool)digitalRead(PIN_startupmode);   
  readEEPROM();                                                       // Reading out EEPROM
  setupWIFI(startupMode);                                             // Start WiFi
  Serial.print(F("Starting webserver..."));            
  server.begin();                                   
  Serial.println(F("[DONE]"));  
  
  Serial.print(F("Booting in ")); 
  if (startupMode) {                                                  // Determine startup mode
    Serial.println(F("SETUP mode"));                                  // Setup mode
    Serial.print(F("Setting up webserver..."));             // Setup Webserver
    WebserverSetupMode();
    Serial.println(F("[DONE]"));          
    display.invertDisplay(true);
  } else {
    Serial.println(F("NORMAL mode"));   // Normal mode
    Serial.print(F("Setting up webserver..."));             // Setup Webserver
    WebserverNormalMode();  delay(100);            // Webserver Normal Mode
    Serial.println(F("[DONE]"));
    connectMQTT();       // MQTT connecting
    display.print(F("Configure WTW..."));  display.display();         // WTW state and Change Filter
    int wtwState = EEPROM.read(eepromWTWaddr);
    if (wtwState == 255) {
      wtwState = 0;
    }
    Serial.println(F("[DONE]"));
    doFilterChange();
    updateWTWstate(wtwState);           // Push initial state to the WTW device (stored in EEPROM)
    display.display();
    delay(2000);
    updateDisplay();
    Serial.println(F("[DONE]"));
    Serial.print(F("MCP Interrupts loading..."));    //MCP Interrupts
    attachInterrupt(PIN_PE_int, doPortExtender, FALLING);
    Serial.println(F("[DONE]"));
  }
  display.display();
  Serial.println(F("initialized")); delay(100);
}

void loop() {
  server.handleClient();               // Handle HTTP (REST) 
  if ((bool)digitalRead(PIN_startupmode) != startupMode) doStartupMode();  // Reboot device is startup mode is changed
  doStartup();
}

void doPortExtender() {
  if (mcp.digitalRead(PIN_button_up)) {buttonUp();  updateWTWstate(buttonState);};
  if (mcp.digitalRead(PIN_button_down)) {buttonDown();  updateWTWstate(buttonState);};
  doFilterChange();
}

void doStartup() {
   if (!startupMode) {   // Handle MQTT    
     if (!mqttClient.connected()) { reconnectMQTT(); } // Connect MQTT if necessary
     if (mqttClient.connected()) {      // Only receive/send if MQTT is actually connected
        mqttClient.loop();              // Receive 
        if ( millis() - lastMQTTmsg > MQTTpublishInterval * 1000) {   // Publish new values on defined interval
          lastMQTTmsg =  millis();
          Serial.println(F("Publish MQTT message"));
          mqttClient.publish(MQTT_State_Topic, String(currentState).c_str());
          mqttClient.publish(MQTT_FilterState_Topic, String(changeFilter).c_str());
        }
     }
     doButtonChange();
     doFilterChange();
  }
}

void doButtonChange() {
  ButtonPinUpState = (bool)mcp.digitalRead(PIN_button_up); 
  ButtonPinDownState = (bool)mcp.digitalRead(PIN_button_down);
  if (ButtonPinUpState && buttonState < buttonStateMax) {
     buttonUp();  
     updateWTWstate(buttonState);
     Serial.print(F("Pin Button up state: "));
     Serial.println(ButtonPinUpState);
  }
  if (ButtonPinDownState && buttonState > buttonStateMin) {
     buttonDown();  
     updateWTWstate(buttonState);
     Serial.print(F("Pin Button Down state: "));
     Serial.println(ButtonPinDownState);
  }
}

void doFilterChange() {
  FilterState = (bool)mcp.digitalRead(PIN_FilterChange);
  if (FilterState) {
    int changeFilter = mcp.digitalRead(PIN_FilterChange);  // Update value
    Serial.print  ("changefilter : ");  
    Serial.println(changeFilter);
    updateDisplay();          //Update display
  }
}

void buttonUp() {
  if (buttonState < buttonStateMax) buttonState = buttonState + 1;       // CW - Clock Wise
}

void buttonDown() {
  if (buttonState > buttonStateMin) buttonState = buttonState - 1;       // CCW - Counter Clock Wise
}

boolean IsNumeric(String str) {
    for(char i = 0; i < str.length(); i++) {
        if ( !(isDigit(str.charAt(i)) || str.charAt(i) == '.' )) {
            return false;
        }
    }
    return true;
}
